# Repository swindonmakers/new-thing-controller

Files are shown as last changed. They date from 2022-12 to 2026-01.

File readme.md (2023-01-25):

Universal WIFI Thing Controller for doing stuff around the makerspace. Machine control, data logging, etc etc.

## Features:
 * Wifi (via Pico W)
 * SPI LCD
 * Resistive touch
 * SD card
 * Buttons
 * WS2812B (onboard + header)
 * 2x relay/contactor coil outputs
 * PN532 NFC card reader header
 * Unusued GPIO expansion

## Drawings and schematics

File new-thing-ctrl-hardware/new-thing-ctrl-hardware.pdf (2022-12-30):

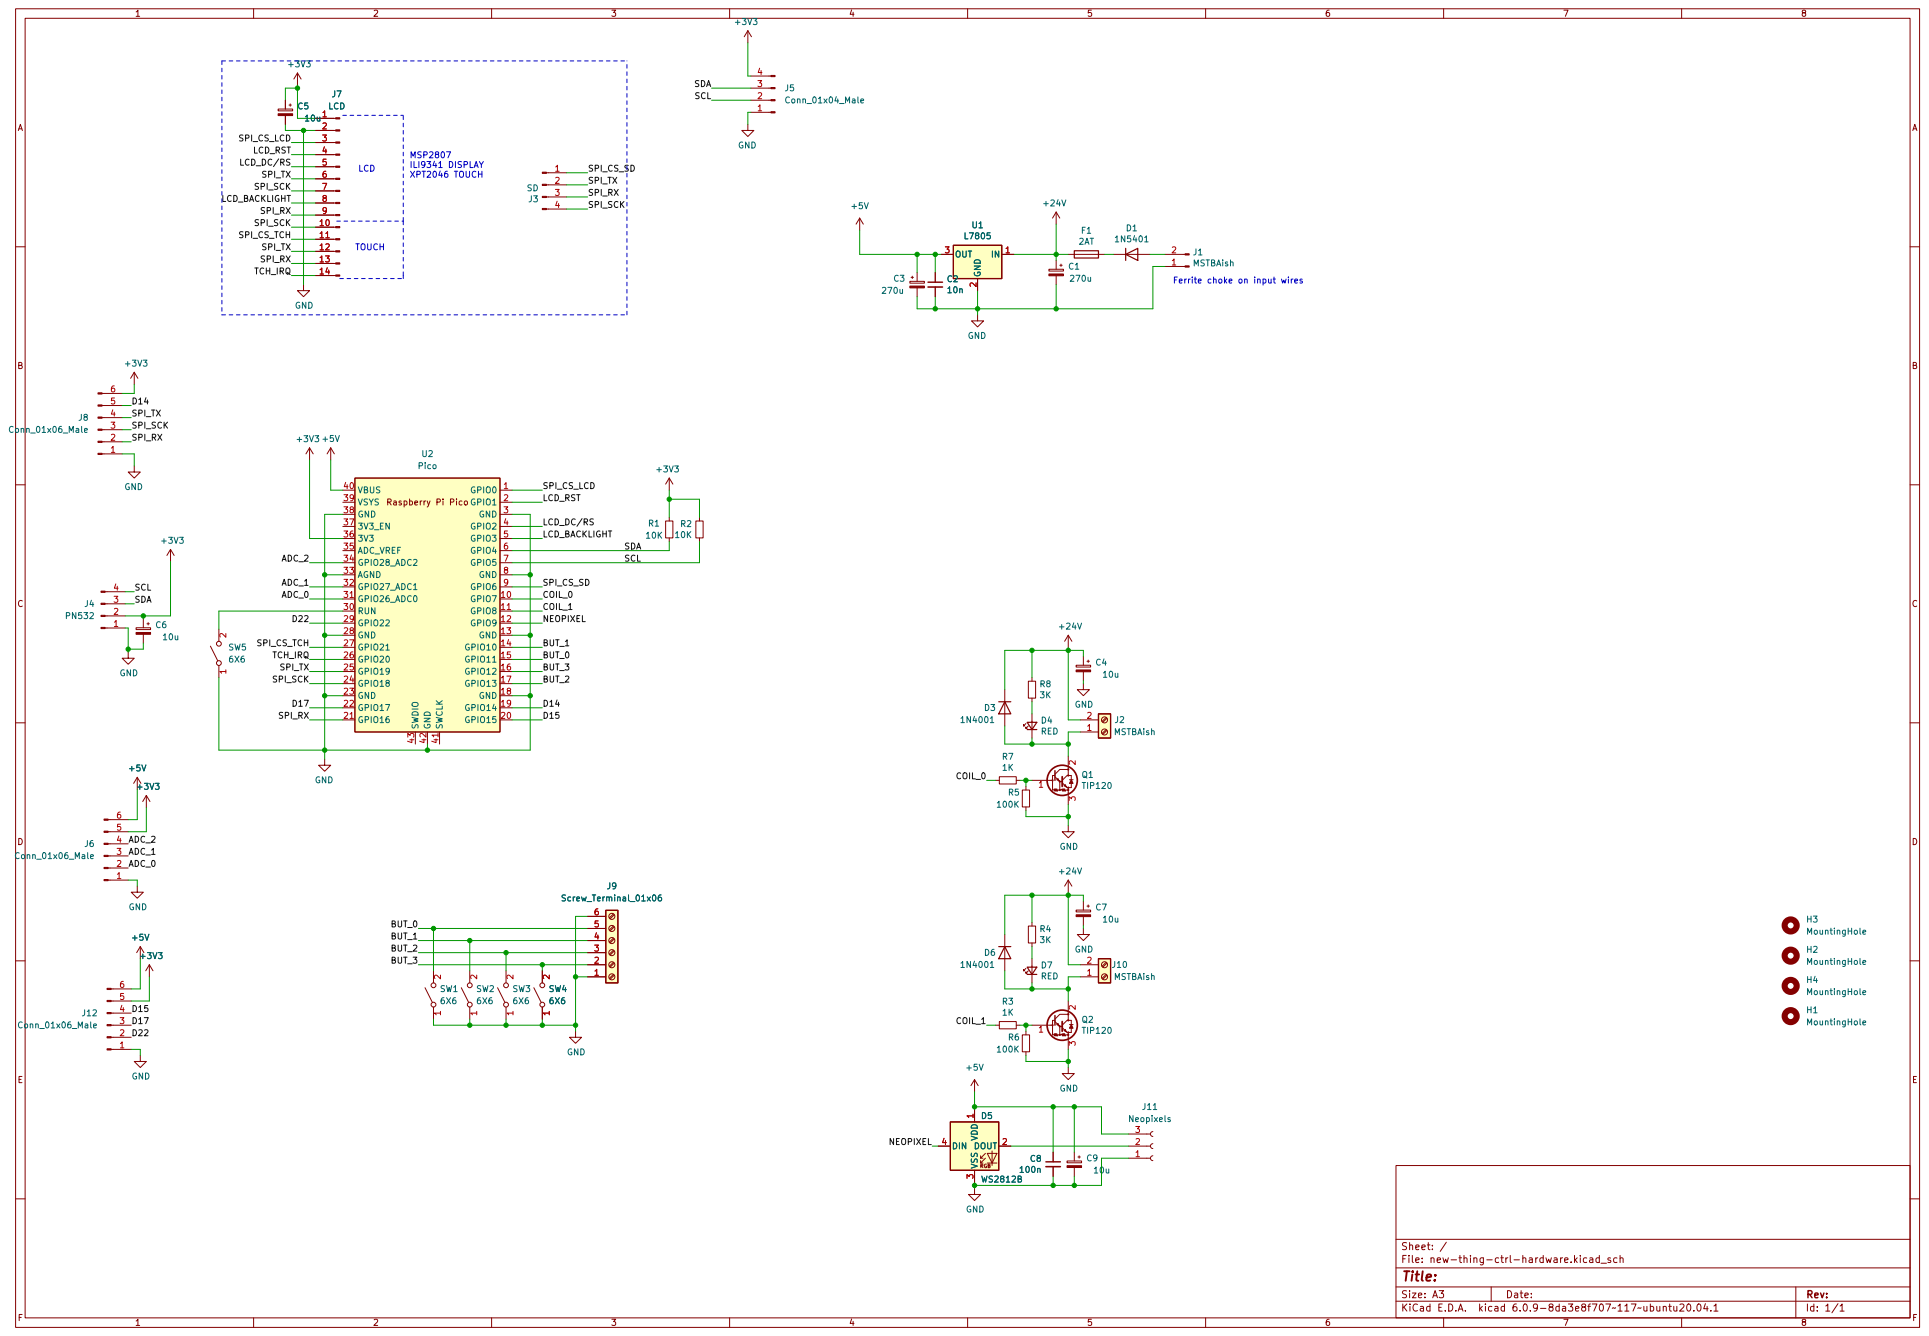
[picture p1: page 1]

4 4
3 3
2 2

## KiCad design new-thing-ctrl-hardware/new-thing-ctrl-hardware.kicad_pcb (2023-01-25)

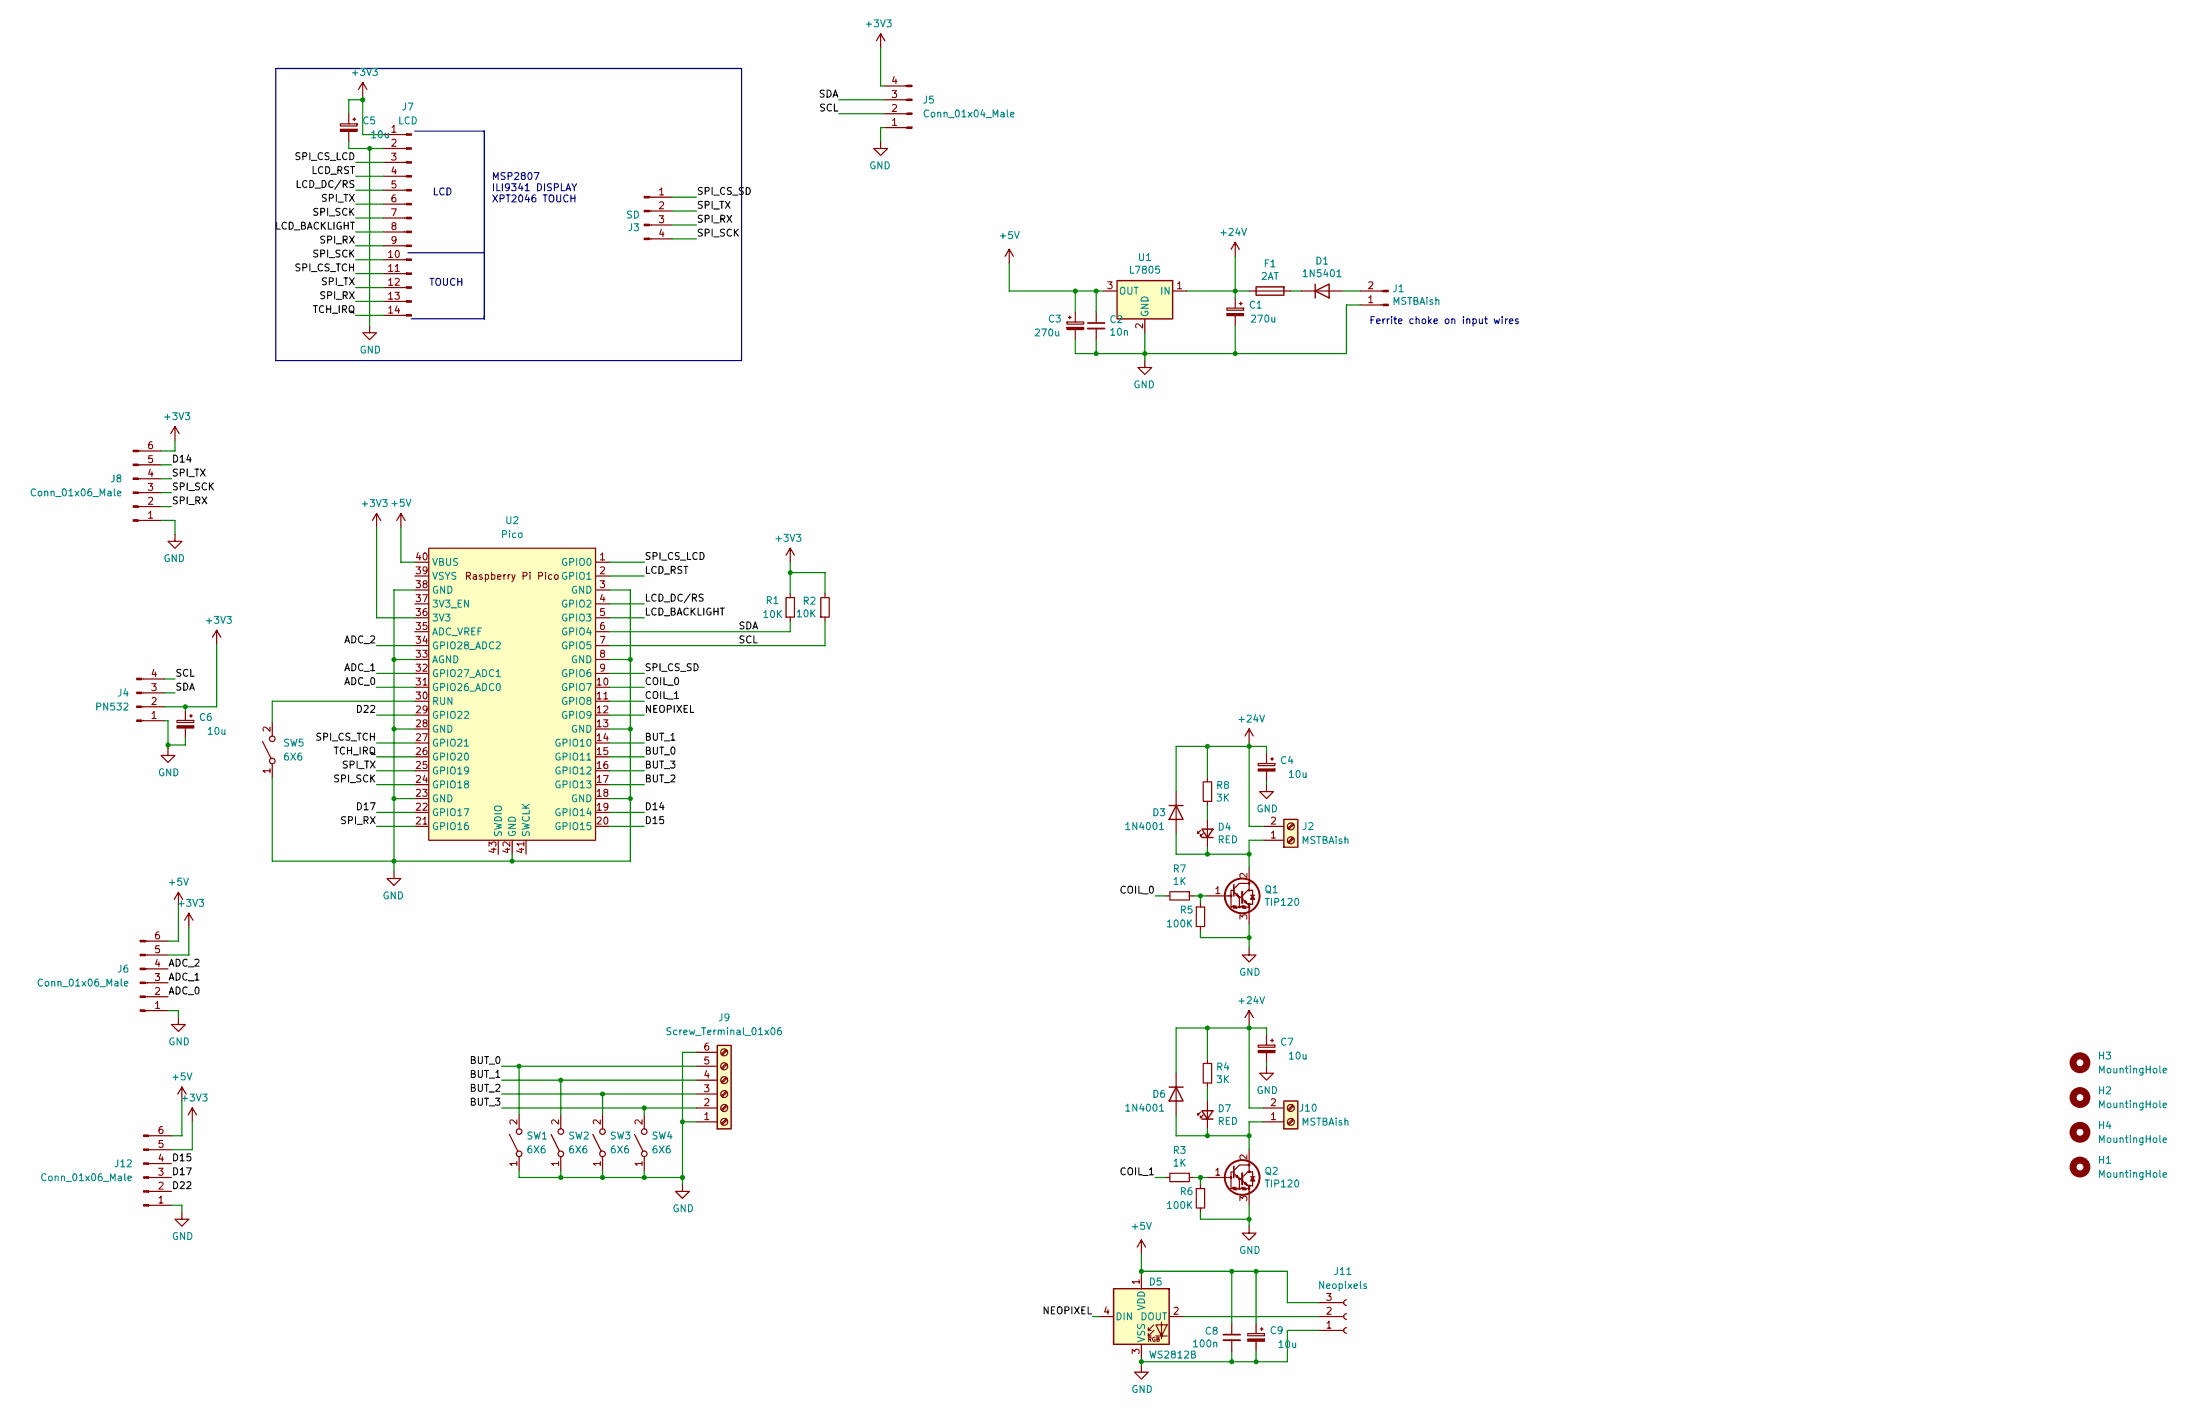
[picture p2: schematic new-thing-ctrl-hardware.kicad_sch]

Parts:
C1, C3: 270u; CP_Radial_D10.0mm_P5.00mm
C2: 10n; C_Disc_D7.0mm_W2.5mm_P5.00mm
C4, C5, C6, C7, C9: 10u; CP_Radial_D5.0mm_P2.50mm
C8: 100n; C_Disc_D7.0mm_W2.5mm_P5.00mm
D1: 1N5401; D_DO-201AD_P15.24mm_Horizontal
D3, D6: 1N4001; D_DO-41_SOD81_P10.16mm_Horizontal
D4, D7: RED; LED_D5.0mm
D5: WS2812B; LED_WS2812B_PLCC4_5.0x5.0mm_P3.2mm
F1: 2AT; Fuseholder_Cylinder-5x20mm_Schurter_0031_8201_Horizontal_Op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
H1, H2, H3, H4: MountingHole; MountingHole_3.2mm_M3
J1, J2, J10: MSTBAish; PhoenixContact_MSTBA_2,5_2-G-5,08_1x02_P5.08mm_Horizontal
J3: SD; PinHeader_1x04_P2.54mm_Vertical
J4: PN532; JST_XH_S4B-XH-A_1x04_P2.50mm_Horizontal
J5: Conn_01x04_Male; JST_XH_S4B-XH-A_1x04_P2.50mm_Horizontal
J6, J8, J12: Conn_01x06_Male; JST_XH_S6B-XH-A_1x06_P2.50mm_Horizontal
J7: LCD; PinHeader_1x14_P2.54mm_Vertical
J9: Screw_Terminal_01x06; PhoenixContact_MSTBA_2,5_6-G-5,08_1x06_P5.08mm_Horizontal
J11: Neopixels; JST_XH_S3B-XH-A-1_1x03_P2.50mm_Horizontal
Q1, Q2: TIP120; TO-220-3_Horizontal_TabDown
R1, R2: 10K; R_Axial_DIN0204_L3.6mm_D1.6mm_P7.62mm_Horizontal
R3, R7: 1K; R_Axial_DIN0204_L3.6mm_D1.6mm_P7.62mm_Horizontal
R4, R8: 3K; R_Axial_DIN0204_L3.6mm_D1.6mm_P7.62mm_Horizontal
R5, R6: 100K; R_Axial_DIN0204_L3.6mm_D1.6mm_P7.62mm_Horizontal
SW1, SW2, SW3, SW4: 6X6; SW_PUSH_6mm_H13mm
SW5: 6X6; SW_PUSH_6mm_H4.3mm
U1: L7805; TO-220-3_Horizontal_TabDown
U2: Pico; RPi_Pico_SMD_TH

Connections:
+3V3: C5.1, C6.1, J4.2, J5.4, J6.5, J7.1, J8.6, J12.5, R1.2, R2.2, U2.36 (3V3)
+5V: C2.1, C3.1, C8.1, C9.1, D5.1 (VDD), J6.6, J11.3, J12.6, U1.3 (OUT), U2.40 (VBUS)
+24V: C1.1, C4.1, C7.1, D3.1 (K), D6.1 (K), F1.1, J2.2, J10.2, R4.2, R8.2, U1.1 (IN)
/ADC_0: J6.2, U2.31 (GPIO26_ADC0)
/ADC_1: J6.3, U2.32 (GPIO27_ADC1)
/ADC_2: J6.4, U2.34 (GPIO28_ADC2)
/BUT_0: J9.5, SW1.2 (B), U2.15 (GPIO11)
/BUT_1: J9.4, SW2.2 (B), U2.14 (GPIO10)
/BUT_2: J9.3, SW3.2 (B), U2.17 (GPIO13)
/BUT_3: J9.2, SW4.2 (B), U2.16 (GPIO12)
/COIL_0: R7.2, U2.10 (GPIO7)
/COIL_1: R3.2, U2.11 (GPIO8)
/D14: J8.5, U2.19 (GPIO14)
/D15: J12.4, U2.20 (GPIO15)
/D17: J12.3, U2.22 (GPIO17)
/D22: J12.2, U2.29 (GPIO22)
/LCD_BACKLIGHT: J7.8, U2.5 (GPIO3)
/LCD_DC/RS: J7.5, U2.4 (GPIO2)
/LCD_RST: J7.4, U2.2 (GPIO1)
/NEOPIXEL: D5.4 (DIN), U2.12 (GPIO9)
/SCL: J4.4, J5.2, R2.1, U2.7 (GPIO5)
/SDA: J4.3, J5.3, R1.1, U2.6 (GPIO4)
/SPI_CS_LCD: J7.3, U2.1 (GPIO0)
/SPI_CS_SD: J3.1, U2.9 (GPIO6)
/SPI_CS_TCH: J7.11, U2.27 (GPIO21)
/SPI_RX: J3.3, J7.9, J7.13, J8.2, U2.21 (GPIO16)
/SPI_SCK: J3.4, J7.7, J7.10, J8.3, U2.24 (GPIO18)
/SPI_TX: J3.2, J7.6, J7.12, J8.4, U2.25 (GPIO19)
/TCH_IRQ: J7.14, U2.26 (GPIO20)
GND: C1.2, C2.2, C3.2, C4.2, C5.2, C6.2, C7.2, C8.2, C9.2, D5.3 (VSS), J1.1, J4.1, J5.1, J6.1, J7.2, J8.1, J9.1, J9.6, J11.1, J12.1, Q1.3 (E), Q2.3 (E), R5.2, R6.2, SW1.1 (A), SW2.1 (A), SW3.1 (A), SW4.1 (A), SW5.1 (A), U1.2 (GND), U2.3 (GND), U2.8 (GND), U2.13 (GND), U2.18 (GND), U2.23 (GND), U2.28 (GND), U2.33 (AGND), U2.38 (GND), U2.42 (GND)
unnamed: D1.1 (K), F1.2
unnamed: D1.2 (A), J1.2
unnamed: D3.2 (A), D4.1 (K), J2.1, Q1.2 (C)
unnamed: D4.2 (A), R8.1
unnamed: D5.2 (DOUT), J11.2
unnamed: D6.2 (A), D7.1 (K), J10.1, Q2.2 (C)
unnamed: D7.2 (A), R4.1
unnamed: Q1.1 (B), R5.1, R7.1
unnamed: Q2.1 (B), R3.1, R6.1
unnamed: SW5.2 (B), U2.30 (RUN)

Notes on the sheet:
LCD
TOUCH
MSP2807 ILI9341 DISPLAY XPT2046 TOUCH
Ferrite choke on input wires

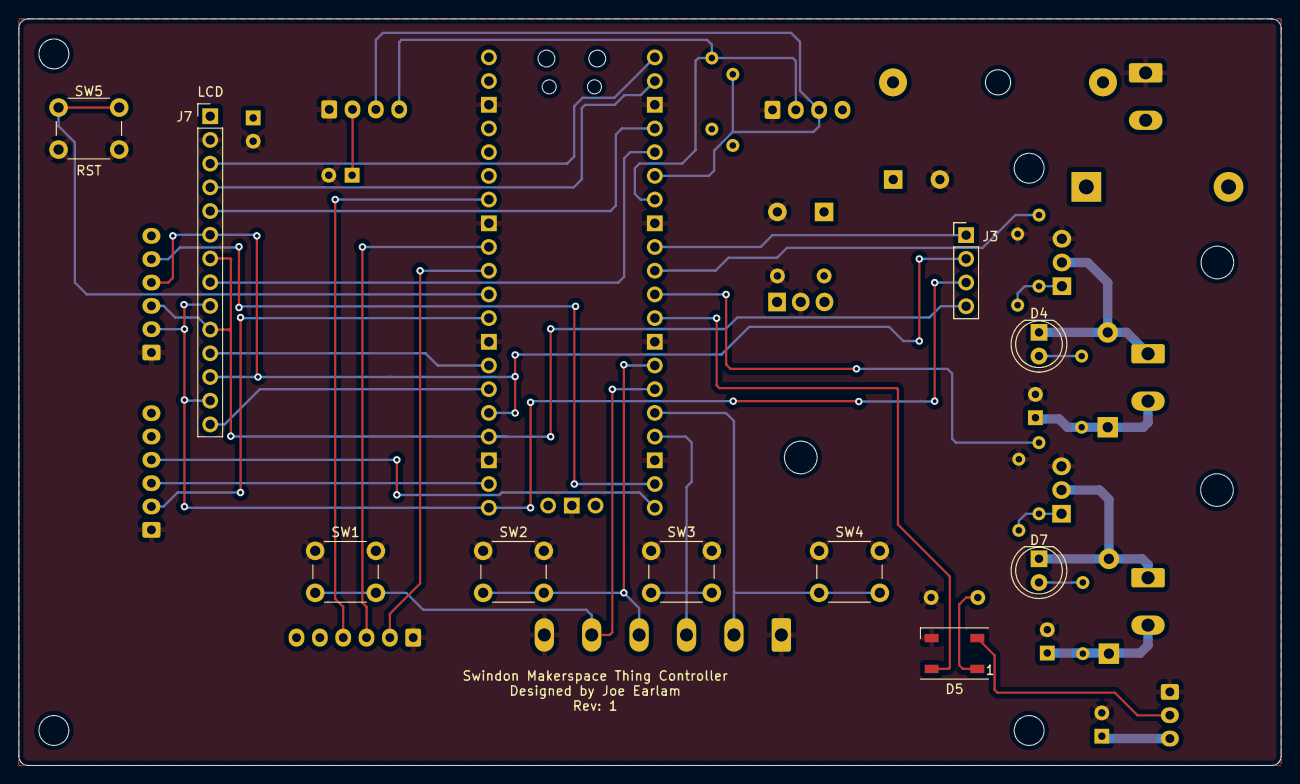
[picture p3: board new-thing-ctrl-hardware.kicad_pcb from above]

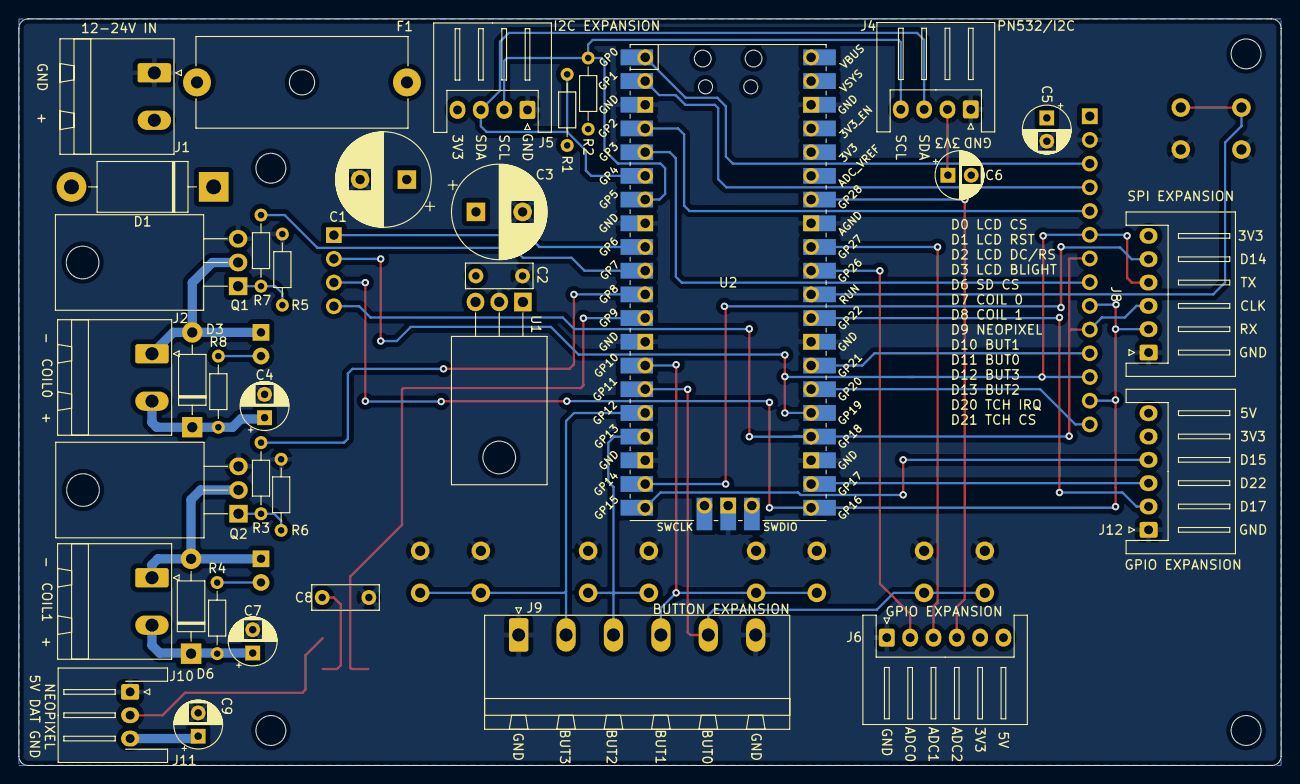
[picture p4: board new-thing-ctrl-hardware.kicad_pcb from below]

Board: 4 copper layers, 135.2 x 80.0 mm, 49 parts (35 on the bottom side), 40 nets.

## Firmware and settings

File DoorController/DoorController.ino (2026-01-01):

//SWINDON MAKERSPACE THING CONTROLLER
// DOOR V0.2

#include "pitches.h"

//DEFINE IF IN WIRED OR WIFI MODE (ONLY 1 define at a time!!!)
//#define WIFIMODE  //UNCOMMENT TO ENABLE WIFI MODE - BOARD SELECTION MUST BE Pi PICO W
#define WIREDMODE   //UNCOMMENT TO ENABLE WIRED MODE - BOARD SELECTION MUST BE Pi PICO or WIZnet W5500-EVB-Pico

#define OVERRIDE_TOKENS

#include "ThingContoller.h"
#ifdef OVERRIDE_TOKENS
    #include "override_tokens.h"
#endif 
//Door IO defines
#define EXIT_BUTTON 13  //INPUT digital GPIO expansion connector pin
#define DOOR_SENSOR 10  //INPUT digital GPIO expansion connector pin


long actionTimer = 0; //time between actions to automate actions in statemachine
long cacheTimer = 0;  //time counter between checking cache (hourly)
long i2c_checker = 0; //I2C appears to crash every so often - check every minute and if fails reset server


enum statemach {
    SM_IDLE,         //waiting for someone swiping to the door
    SM_UNLOCK,       //door access granted or door unlock pressed
    SM_RESPONSE,     //door access denied
    SM_REMAINS_OPEN  //door has been left open 
};


void gotoSM_IDLE();
void gotoSM_UNLOCK();
void gotoSM_RESPONSE();
void gotoSM_REMAINS_OPEN();
void alert_user();
void play_alert();

#define REST      0
// so -4 means a dotted quarter note, that is, a quarter plus an eighteenth!!
int melody[] = {
  NOTE_E4,4, NOTE_B3,4, REST,2,
  NOTE_E4,4, NOTE_B3,4, REST,2,
  NOTE_E4,4, NOTE_B3,4 
 
};

statemach thingState = SM_IDLE;
int i=0;
void setup() {
    pinMode(EXIT_BUTTON, INPUT_PULLUP);
    pinMode(DOOR_SENSOR, INPUT_PULLUP);
    pinMode(BUZZER, OUTPUT);
    printHeadline("Booting Up");
    #ifdef OVERRIDE_TOKENS
      populate_override_tags();//do before setup so tags can be used during setup
    #endif 
    thing_setup();
    showLogo();
    delay(1000);
    printHeadline("Booted up");
    rp2040.wdt_begin(8000);
    

    gotoSM_IDLE();
    sendServerLogMsg(Thing_Name + " Booted Sucessfully!");
//    Verbosity = VERB_HIGH;
};

void loop(){
    rp2040.wdt_reset(); //reset watchdog
    RFID_TAG tag;
    getRFID_tag(&tag); //see if there is a RFID tag present
    if (tag.valid == true){ //if tag found
        SM_ACCOUNT account;
        account.tag = tag;
        #ifdef OVERRIDE_TOKENS
        if (is_override_tag(tag)){
            gotoSM_UNLOCK();
            colourPattern = PATTERN_PYB;
            TFTLcd_setIconColour(ILI9341_WHITE);
            printTitle("OVERRIDE");
            sendServerLogMsg("Override Key Used", uid2String(tag.uid, tag.uid_length));
        }else{
        #endif
            if (checkIfInStoredAccounts(&account))
            {
                printBody_update("got from cache",false);
            }else{
                //not in cache check server
                getSMAccountFromServer(&account);
                if (account.flags & TOKEN_CACHE){
                    addToStoredAccounts(account);
                }
            }
            colourPattern = account.colour;
            if (account.flags & TOKEN_ACCESS)
            {
                gotoSM_UNLOCK();
                printHeadline_update("Valid Tag", false);
                printBody_update("Welcome", false);
                printBody_update(account.Name, true);
                TFTLcd_setIconColour(ILI9341_GREEN);
                sendServerLogMsg("Access Granted to :" + String(account.Name) , uid2String(account.tag.uid, account.tag.uid_length));
            }
            else
            {
                gotoSM_RESPONSE();
                printHeadline("Access Denied");
                if (account.Name[0] == 0 )//if no name
                {
                    sendServerLogMsg("Access Denied to" , uid2String(account.tag.uid, account.tag.uid_length));
                } else{
                    sendServerLogMsg("Access Denied to :" + String(account.Name) ,uid2String(account.tag.uid, account.tag.uid_length));
                }
            }
            if (account.flags & TOKEN_BEEP){
              play_alert();
            }
            animate_leds(); //force led update immidiately so that it changes colour before waiting on parking cars
            //tell server to park car - no matter if they have access or not
//             String park_json = sendServerCustomMsg("park", "", uid2String(tag.uid, tag.uid_length), "", true);
//             if (!(park_json == "")){
//               DynamicJsonDocument jsonBuffer(200);
//               deserializeJson(jsonBuffer,park_json);
//               JsonObject root = jsonBuffer.as<JsonObject>();
//               if (root.isNull()) {
//                 printBody("Parking Error");
//                 printBody("Msg Directors");
//               }
//               if (root.containsKey("message")) {
//                 printBodyLong(root["message"]);
//               }
//               if (root.containsKey("notparked")) {
//                 play_alert();
//                 printBodyLong(root["notparked"]);
//               }              
//               if (root.containsKey("error")){
//                 //play_alert();
// //                printBodyLong(root["error"]);
//                 printBody("No cars registered");
//               }
              
//             }
        #ifdef OVERRIDE_TOKENS
        }
        #endif
    }
    
    //statemachine logic

    switch (thingState){
        case SM_IDLE:
            if (digitalRead(DOOR_SENSOR)){//if door is open for no reason
                gotoSM_REMAINS_OPEN();
            }
            if (!digitalRead(EXIT_BUTTON)){//if someone wants to leave
                gotoSM_UNLOCK();
                colourPattern = PATTERN_PINK;
                printBody("Unlocking by Button");
            }
            break;
        case SM_UNLOCK:
            if(actionTimer + (Unlock_Seconds*1000) < millis()){//if door has stayed open long enough
                if (digitalRead(DOOR_SENSOR)){ //door still open
                    gotoSM_REMAINS_OPEN();
                }else{ //door closed go to idle
                    gotoSM_IDLE();
                }
            }
            break;
        case SM_RESPONSE:        
            if(actionTimer + (Unlock_Seconds*1000) < millis()){//if door has stayed open long enough
                gotoSM_IDLE();
            }  
            break;                  
        case SM_REMAINS_OPEN:
            if (!digitalRead(DOOR_SENSOR)){
                gotoSM_IDLE();
            }
            break;

    }


    if (millis() > (cacheTimer + 3600000)){
        //once every hour check membership cache 
        updateStoredAccounts();
        cacheTimer = millis();
    }

    // if (millis() > (i2c_checker) + 61000){
    //     printBody("checking i2c bus");
    //     uint32_t versiondata = nfc.getFirmwareVersion();
    //     if (versiondata == 0)
    //     {
    //         printBody("FAILED TO REACH NFC");
    //         printTitle("ERROR!");
    //         printBody("reseting in a few seconds");
    //         sendServerLogMsg("Oh No, the RFID tag reader isnt responding, reseting in a moment to see if that helps");
    //         while(1){
    //             delay(1000);
    //         }
    //     }
    //     i2c_checker = millis();
    //     actionTimer = millis();
    // }



    animate_leds();//animate the spiral effect

 
    if (millis() > actionTimer + 30000)//if 30 seconds of inactivity
    {
        if(bodyMsg[LCD_NUM_LINES-1] != "")//if screen isnt already blank 
        {
            printBody("Clearing Screen");
            delay(1000);
            for (int i = 0; i < LCD_NUM_LINES; i++)
            {
                //    printBody(String(i));
                bodyMsg[i] = "";
            }
            printBody("");//update screen(s)
            if (text_lcd_enabled) //turn of led backlight
                Textlcd.noBacklight();
        }
    }
}

void gotoSM_IDLE(){
    thingState = SM_IDLE;
    colourPattern = PATTERN_ORANGE;
    printHeadline("Scan a Tag");
    lockDevice();//lock door only once closed
    actionTimer = millis(); 
}
void gotoSM_UNLOCK(){
    unlockDevice();
    thingState = SM_UNLOCK;
    actionTimer = millis();
}
void gotoSM_RESPONSE(){
    thingState = SM_RESPONSE;
    actionTimer = millis();
}
void gotoSM_REMAINS_OPEN(){
    thingState = SM_REMAINS_OPEN;
    colourPattern = PATTERN_PINK;
    if (headlineMsg != "Door is open"){//update display to say its open if it isnt right now
        printHeadline("Door is open");
    }
}

void play_alert(){
  int notes = sizeof(melody) / sizeof(melody[0]) / 2;
  int tempo = 140;
  
  // change this to whichever pin you want to use
  int buzzer = 11;
  // this calculates the duration of a whole note in ms
  int wholenote = (60000 * 2) / tempo;
  
  int divider = 0, noteDuration = 0;
    for (int thisNote = 0; thisNote < notes * 2; thisNote = thisNote + 2) {
      rp2040.wdt_reset(); //reset watchdog
      // calculates the duration of each note
      divider = melody[thisNote + 1];
      if (divider > 0) {
        // regular note, just proceed
        noteDuration = (wholenote) / divider;
      } else if (divider < 0) {
        // dotted notes are represented with negative durations!!
        noteDuration = (wholenote) / abs(divider);
        noteDuration *= 1.5; // increases the duration in half for dotted notes
      }
  
      // we only play the note for 90% of the duration, leaving 10% as a pause
      tone(BUZZER, melody[thisNote], noteDuration*0.9);
  
      // Wait for the specief duration before playing the next note.
      delay(noteDuration);
      
      // stop the waveform generation before the next note.
      noTone(BUZZER);
    }
   
}

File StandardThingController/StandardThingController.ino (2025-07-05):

//SWINDON MAKERSPACE THING CONTROLLER
// DOOR V0.1
#define SOFTWARE_VER "1.2"
#define SOFTWARE_TYPE "Standard"

//DEFINE IF IN WIRED OR WIFI MODE (ONLY 1 define at a time!!!)
#define WIFIMODE  //UNCOMMENT TO ENABLE WIFI MODE - BOARD SELECTION MUST BE Pi PICO W
//#define WIREDMODE   //UNCOMMENT TO ENABLE WIRED MODE - BOARD SELECTION MUST BE Pi PICO or WIZnet W5500-EVB-Pico

// #define OVERRIDE_TOKENS

#define ACTIVATE_BUTTON 11
#define SIGNOUT_BUTTON 10
#define INDUCT_BUTTON 12
#define ACTIVATE_LED 22
#define SIGNOUT_LED 17
#define INDUCT_LED 15
#define SCREEN_ROTATION 1

#include "ThingContoller.h"
#ifdef OVERRIDE_TOKENS
    #include "override_tokens.h"
#endif 

long actionTimer = 0; //time between actions to automate actions in statemachine
long logout_timer = 0;
long tool_on_timer = 0; //start time value of when device is turned on 
long continued_on_timer = 0; //helps track time intervals to see if device is still on
int  idle_timeout = 0;
long debug_timer = 0; //count how long the debug button has been pressed for
bool debug_btn_state = false;

enum statemach {
    SM_SIGNED_OUT,        //waiting for someone swiping to sign in
    SM_SIGNED_IN,         //unlocked but machine not turned on yet
    SM_THING_ACTIVE,      //machine active
    SM_INDUCTING,         //inductor has signed in and inducting someone
    SM_OTA_DEBUG          //Hidden menu, enter to see debug info + enable OTA mode
};

void gotoSM_SIGNED_OUT();
void gotoSM_SIGNED_IN();
void gotoSM_THING_ACTIVE();
void gotoSM_INDUCTING();
void gotoSM_OTA_DEBUG();

SM_ACCOUNT account;
statemach thingState = SM_SIGNED_OUT;

void setup() {
  printHeadline("Booting Up");
  thing_setup();
  showLogo();
  delay(500);
  printHeadline("Booted up");
  rp2040.wdt_begin(8000);

  gotoSM_SIGNED_OUT();
  sendServerLogMsg(Thing_Name + " Booted Sucessfully!");

  pinMode(ACTIVATE_BUTTON, INPUT_PULLUP);
  pinMode(SIGNOUT_BUTTON, INPUT_PULLUP);
  pinMode(INDUCT_BUTTON, INPUT_PULLUP);
  pinMode(ACTIVATE_LED, OUTPUT);
  pinMode(SIGNOUT_LED, OUTPUT);
  pinMode(INDUCT_LED, OUTPUT);
  actionTimer = millis();
  Verbosity = VERB_NORMAL;
}

void loop() {
  rp2040.wdt_reset(); //reset watchdog
  RFID_TAG tag;
  switch (thingState){
    case SM_SIGNED_OUT:
      getRFID_tag(&tag); //see if there is a RFID tag present
      if (tag.valid == true){
        actionTimer = millis();
        account.tag = tag;
        if (checkIfInStoredAccounts(&account))
        {
          printBody("got from cache");
        }else{
          getSMAccountFromServer(&account);
          if (account.flags & TOKEN_CACHE){
              addToStoredAccounts(account);
          }
        }

        colourPattern = account.colour;
        if (account.flags & TOKEN_ACCESS)
        {
          gotoSM_SIGNED_IN();
          printBody_update("Welcome",false);
          printBody(account.Name);
          sendServerLogMsg("Access Granted to :" + String(account.Name) , + "to " + Thing_Name);
        }
      }
      if(actionTimer + (Unlock_Seconds*1000) < millis()){
        colourPattern = PATTERN_ORANGE;
      };

      //debug mode check
      if(!digitalRead(INDUCT_BUTTON)){
        if(debug_btn_state == false){
          debug_btn_state = true;
          debug_timer = millis();
        }else{
          if(debug_timer + 5000 < millis()){
            gotoSM_OTA_DEBUG();
          }
        }
      }

      break;//SM_SIGNED_OUT
      
    case SM_SIGNED_IN:
      if (!digitalRead(SIGNOUT_BUTTON)){
        gotoSM_SIGNED_OUT();
        break;
      }
      if (!digitalRead(ACTIVATE_BUTTON)){
        gotoSM_THING_ACTIVE();
        while(!digitalRead(ACTIVATE_BUTTON))
          {delay(50);}
        delay(50);
        break;
      }
      if (account.flags & TOKEN_INDUCTOR){
        if (!digitalRead(INDUCT_BUTTON)){
          gotoSM_INDUCTING();
          break;
        }
      } 
      
      if (continued_on_timer + 60000 < millis()){
        continued_on_timer += 60000;
        idle_timeout--;
        actionTimer = millis();//prevent screen clearing
        switch (idle_timeout){
          case 10: 
            printBody("Auto Logout in 10 Mins");
            break;
          case 5: 
            printBody("Auto Logout in 5 Mins");
            break;
          case 3: 
            printBody("Auto Logout in 3 Mins");
            break;
          case 2: 
            printBody("Auto Logout in 2 Mins");
            break;
          case 1: 
            printBody("Auto Logout in 1 Min");
            break;
          case 0: 
            printBody("Logout due to inactivity");
            gotoSM_SIGNED_OUT();
            break;
        }        
      }
      break; //SM_SIGNED_IN

    case SM_THING_ACTIVE:
      if (!digitalRead(ACTIVATE_BUTTON)){
        gotoSM_SIGNED_IN();
        break;
      }
      if (!digitalRead(SIGNOUT_BUTTON)){
        gotoSM_SIGNED_OUT();
        break;
      }
      if (continued_on_timer + 300000 < millis()){
        continued_on_timer += 300000; //not millis as this will keep it in time better
        long active_time = millis() - tool_on_timer;
        printBody("Still on for " + String(active_time/1000) + " Seconds");    
        sendServerUptimer(uid2String(account.tag.uid, account.tag.uid_length), "1", Thing_Name + " still being used by " + account.Name, String(active_time/1000));
        actionTimer = millis();
      }      
      break;
    case SM_INDUCTING:
      getRFID_tag(&tag); //see if there is a RFID tag present
      if (!digitalRead(INDUCT_BUTTON)){
        gotoSM_SIGNED_IN();
        break;
      }
      if (!digitalRead(SIGNOUT_BUTTON)){
        gotoSM_SIGNED_OUT();
        break;
      }      
      if (tag.valid == true){
        sendServerInduction(uid2String(account.tag.uid, account.tag.uid_length), uid2String(tag.uid, tag.uid_length));
        printBody("tag inducted");
        actionTimer = millis();
      }
      break;//SM_THING_ACTIVE

    case SM_OTA_DEBUG:
      ArduinoOTA.handle(); //check for OTA updates
      if(!digitalRead(INDUCT_BUTTON)){
        if(debug_btn_state == false){
           gotoSM_SIGNED_OUT();
        }
      }else{
        debug_btn_state = false;
      }
      if(!digitalRead(ACTIVATE_BUTTON)){
        Verbosity++;
        if (Verbosity > VERB_MAX)
          Verbosity = 0;
        gotoSM_OTA_DEBUG(); //refresh screen
        while(!digitalRead(ACTIVATE_BUTTON)) //wait until button is depressed
          {delay(50);}
        delay(50);
      }

      delay(10);
      actionTimer = millis(); //dont clear the screen in this state
      break;//SM_OTA_DEBUG

  }
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

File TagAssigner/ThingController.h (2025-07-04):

// Base code for the thing controller, contains useful code required by all types of thing controllers in the makerspace from door to tool, etc

// TODO TEXTLCD support

// required libraries
#include "SPI.h"              //hardware SPI for display
#include <Adafruit_GFX.h>     //draw things on the display
#include <Adafruit_ILI9341.h> //display
#include <LittleFS.h>         //File system
#include "Adafruit_PN532.h"   //RFID reader USE VERSION 1.2.2!!!!!!!
#include <FastLED.h>          //addressable RGB led control
#include <ArduinoJson.h>      //json parser
#include <LiquidCrystal_I2C.h>//4x20 lcd display
#ifdef WIFIMODE               // wifi libraries
#include <WiFi.h>
#endif
#ifdef WIREDMODE // wired libraries
#include <Ethernet_Generic.h>
#include <ArduinoUniqueID.h>
#endif

//text lcd display dimensions
#define LCD_COLS 20
#define LCD_ROWS 4
const uint8_t i2cAddr = 0x27;
LiquidCrystal_I2C Textlcd = LiquidCrystal_I2C(i2cAddr, 20, 4); // Change to (0x27,20,4) for 20x4 LCD.

// ILI9341 pinout defines
#define TFTLCD_CS 0
#define TFTLCD_DC 2
#define TFTLCD_MOSI 19
#define TFTLCD_CLK 18
#define TFTLCD_RST 1
#define TFTLCD_MISO 16
#define TFTLCD_BACKLIGHT 3
#define I2C_IRQ 14    // Might change in rev 2 of board placeholder if this happens
#define RFID_RESET 27 // not connected but needed in code
#define ETHERNET_RESET 20

// NFC reader control properties
#define CARD_DEBOUNCE_DELAY 2000 // milliseconds between successful card reads
#define PN532_READ_TIMEOUT 50    // milliseconds

// rgb addressable led
#define BRIGHTNESS 160
#define LED_TYPE WS2812B
#define COLOR_ORDER GRB
#define LED_PINOUT 9
int NUM_LEDS = 0; // number of RGB leds, if 0 then disable
CRGB *leds;       // led colour array

// colour patterns - matching value arriving in JSON from server for what colur to display
#define PATTERN_WHITE 0
#define PATTERN_GREEN 1
#define PATTERN_PURPLE 2
#define PATTERN_BLUE 3
#define PATTERN_PINK 4
#define PATTERN_ORANGE 5
#define PATTERN_RAINBOW 17
#define PATTERN_PYB 18
#define PATTERN_RED 32     // 32 and higher are error colours
#define PATTERN_REDBLUE 33 // half red half blue
#define PATTERN_REDORANGE 34
#define PATTERN_REDGREEN 35
#define PATTERN_REDPURPLE 36
#define PATTERN_REDPINK 37
#define PATTERN_REDWHITE 38
int colourPattern = 0; // led state

//flags for swindonmakerspace account information
#define TOKEN_ACCESS 0x01    //bit0 in flags
#define TOKEN_CACHE 0x02     //bit1 in flags
#define TOKEN_INDUCTOR 0x04  //bit2 in flags
#define TOKEN_DIRECTOR 0x08  //bit3 in flags (not yet used)
#define TOKEN_READ 0x10      //bit4 in flags (card seen but no access)

// setup devices
Adafruit_ILI9341 TFT_lcd = Adafruit_ILI9341(&SPI, TFTLCD_DC, TFTLCD_CS, TFTLCD_RST); // Colour LCD
Adafruit_PN532 nfc(I2C_IRQ, RFID_RESET);                                             // rfid tag reader

bool TFT_lcd_enabled = false;  // if this thing has a colour lcd
bool serial_enabled = false;   // if this thing should output information on the serial port
bool text_lcd_enabled = false; // if this thing has a 4x20 LCD text display

// output pin signal of the thing that is being contolled
int thingPin = 7;              // output pin of the thing being controller (default 7)
PinStatus thingOnState = HIGH; // default output value to enable the machine

// symbols to show on the 4x20 LCD
byte LOCKED_SYMBOL[] = {0b01110, 0b10001, 0b10001, 0b11111, 0b11011, 0b11011, 0b11111, 0b00000};
byte UNLOCKED_SYMBOL[] = {0b01110, 0b10000, 0b10000, 0b11111, 0b11011, 0b11011, 0b11111, 0b00000};

// Msg information. Needed to show text reliably on ILI9341
#define LCD_NUM_LINES 10
String titleMsg;
String headlineMsg;
String bodyMsg[LCD_NUM_LINES];
uint16_t titleColour = ILI9341_WHITE;
uint16_t headlineColour = ILI9341_WHITE;
uint16_t bodyColour = ILI9341_WHITE;

// network settings (wired or wireless)
//  configured later from json on littleFS
IPAddress ip{IPAddress(192, 168, 1, 252)}; // default, gets set later
String Server_Host = "";
int Server_Port = 0;
String Server_URLPrefix = "";
int wifi_error_count = 0; // if gets to 3 then reset device as its probably a wifi issue
#ifdef WIFIMODE
                          // Wifi specific IDs
String Network_SSID = "";
String Network_Password = "";
#endif
byte macAddr[6] = {0, 0, 0, 0, 0, 0}; // Wired only? gets set later

// device settings
String Thing_ID = "";
String Thing_Name = "";
int Unlock_Seconds = 5; // time staying unlocked

typedef uint8_t RFID_token[7]; // value in an rfid tag

// RFID tag information
struct RFID_TAG
{
    char uid[14];
    uint8_t uid_length = 0;
    uint8_t valid = 0;
};

// Swindon Makerspace Account information
struct SM_ACCOUNT
{
    char Name[20] = "NULL";     // name
    uint8_t flags = 0;          // action flags
    uint8_t colour = 0;         // access colour pattern
    uint8_t store_counter = 24; // decrement every hour and once 0 remove from cache
    RFID_TAG tag;
};
#define STORAGE_TIME 24 //number of hours to store an account

#define STOREDACCOUNTSNUM 64
SM_ACCOUNT stored_accounts[STOREDACCOUNTSNUM];
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

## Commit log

2022-12-29 ready for review and manufacture
    [new-thing-ctrl-hardware.kicad_pcb, new-thing-ctrl-hardware.kicad_sch]
2022-12-30 changed some connector footprints, added reset button
    [new-thing-ctrl-hardware.kicad_pcb, new-thing-ctrl-hardware.kicad_sch]
2023-01-25 implemented SPI display
    [new-thing-ctrl-hardware.kicad_pcb]
2023-02-07 LCD + taskscheduler arduino test code
2024-03-05 pinout update + i2c recovery
    updated pinout to match real world
    added i2c crash recovery to see if that fixes the door going unresponsive
    [DoorController.ino, ThingContoller.h]
2024-04-10 Improved ethernet stability
    Added reset of ethernet controller on boot, controller sometimes fails to wake up correctly after power cut, this should help address that be hard reseting after the power has come back before initialising to make sure its ready to use
    [DoorController.ino, ThingContoller.h]
2024-08-26 Standard thing controller added
    Standard thing controller is for most tools. You need to edit the tool name, UUID, and network settings in data folder to connect correctly
    [StandardThingController.ino, ThingContoller.h]
2025-07-04 Prep for Door controller to handle parking
    Prep for Door controller to handle parking and a few minor fixes to other controllers
    [DoorController.ino, StandardThingController.ino, TagAssigner.ino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]
2025-07-04 Added verbosity of debug messages
    an initial attempt to help understand why the thing controllers are randomly failing to parse jsons sent from the server
    [StandardThingController.ino, ThingContoller.h]
